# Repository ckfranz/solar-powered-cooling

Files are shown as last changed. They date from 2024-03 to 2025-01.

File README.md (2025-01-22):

Solar Tracker

# Automated Solar Powered Cooling

The course project involved designing a prototype for a solar tracking solar cell-powered fan cooling system.
<p align="center">
Screenshot 2025-01-21 at 10 57 51 PM
</p>

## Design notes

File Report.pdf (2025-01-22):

## SYDE 361

Nicholas Barton (20877569), Jack Eshkenazi (20893647), Greg Fouzie (20889968), Curtis Franz (20831938), Azaan Wazir (20877312)

## Prototype - Solar Panel Powered Fan Components 2-4

SYDE361-S2023 2

Component 2: Insights

Insight #1: When building the initial prototype, there was an issue of there not being enough space to place all electrical components securely within the product.

Method: The design team was able to find this issue by initially attempting to place all the components and seeing that they did not all fit.

Application: The team measured the dimensions of all the components to see if there was any feasible method to place all the parts within the container. Realizing that the electrical components did not all fit in the design, the team decided to redesign the electrical container. The container was bound horizontally such that it had to fit within an existing piece, so the piece was expanded vertically to allow more components to sit inside. This insight applies to the project as this forced a change to the aesthetics of the design. Previously, the component box was small and didn’t stick out when being used, but now with the longer container the electrical container stuck out. The team could address this in later design iterations by making the bounding component larger horizontally or extending the container base vertically such that when tilted the electrical container doesn’t stick out.

Insight #2: The initial fan cage that was designed was no longer required for the prototype.

Method: The team found the originally designed fan cage to be unnecessary, due to the fan being slow and therefore not harmful to the user. This was discovered by gradually increasing the fan speed through increasing current and testing the force exerted on the test user’s hands. Once the upper bound of the producible fan speed was reached, the team was able to derive that it wouldn’t cause any pain when interacting with the fan.

Application: This insight was useful for the project to help simplify the physical complexity of the design and allow for the product to be built in the limited time that was given. In future designs and iterations, the team will need to find out the theoretical max current output of the panel and the max rotations per minute of the fan in the final design. Using research and analysis the team can find out whether the fan will be damaging or dangerous to the user. The fan cage will then be implemented as planned should there be any danger.

Insight #3: The summer season tilt angle of the solar panel could not be reached using the device which did not properly allow the solar panel to have the correct tilt angle for all seasons.

Method: The team was able to find this issue during the initial testing. When the team attempted to test all the seasonal configurations (tilt angles) of the solar panel, the rotation of the solar panel was blocked due to its platform being too long. This led to the rotation being stopped and the summer tilt angle being unreachable.

Application: This insight applies to the project since it directly impacts the design of the prototype. This impacted the design by forcing the team to decrease the solar panel platform length. The redesign did not change the overall look of the design, but it did make it harder to attach pieces together. The surface area for the command strips was smaller which led to having less grip between the components. Overall, the prototype still functioned reliably, but for future iterations where parts could be scaled, all tilt angles should be simulated before being tested physically to ensure functionality without risking redesign.

Component 3: Prototype Verification

The principal objective of data collecting was to gain insight in two particular areas. The first was to determine the degree to which different levels of cloud cover affect the maximum theoretical power output. The second was to determine how light-based tracking affects the maximum theoretical power output.

Three unique sets of data were collected (Table 3.1). All tests were performed at the same picnic bench near the north entrance to E5. In each test, the system was placed on top of the picnic bench such that the solar panel was exposed to the sky with no obstructions. The angle of elevation of the solar panel was set to 20° which corresponds to the 4th position of the adjustment wheel, optimal for June-September in Waterloo (see figure 4.1). Finally, a fine sampling period of 0.5 seconds was used to capture transient changes in the metrics being collected.

Table 3.1 - Testing Conditions

| Test 1 | Test 2 | Test 3
Date. time | 13/07/23, 2:30-3 pm | 16/07/23, 2:30-3 pm | 16/07/23, 3-3:30 pm
Sun condition | Cloudy | Partly Sunny/Hazy | Partly Sunny/Hazy
Tracking System | Single Axis Tracking | Single Axis Tracking | Fixed

Figure 3.1 compares the maximum theoretical power yields of the solar panel in cloudy versus sunny conditions. From about 2:30 to 2:57 pm, there is a significant amount of variation in maximum theoretical power yields in both plots due to transient changes in the sun conditions due to clouds and cloud breaks. However, from 2:43 to 2:57 pm there is a clear disparity in maximum theoretical power yields. During this timeframe, the respective sun conductions held mostly steady. Here, test 2 (mostly sunny conditions) had theoretical power yields of approximately 250mW, around 5x, the theoretical power yields of test 1 (mostly cloudy conditions), which hovered around 50mW. This deviation shows how significantly power yields are affected by cloud conditions. This information would be useful to communicate to users in a user manual to inform them when and what sun conditions the system can realistically be used to power the fan. This result would also be valuable to consider in future design iterations in the development of power-saving features.

Interestingly, there are a couple of maximum theoretical power spikes in the test 1 plot where the sun broke out. At 2:58 pm the theoretical maximum power levels reached a peak of 551mW. This exceeded the maximum theoretical power observed over the entire duration of test 2 (mostly sunny conditions), due to some haziness during test 2.

Figure 3.2 compares the maximum theoretical power yields of the solar panel with and without single-axis tracking. In test 2, the panel utilizes a pair of photoresistors to orient the panel such that it receives optimal light exposure. While the first 13 minutes of test 2 depict varying sun exposure due to fleeting clouds, the maximum theoretical power peaks over the course of the entire interval remain fairly steady (around 250mW). In test 3, the panel was fixed at the optimal azimuth the moment the testing interval began. As time passed and the sun’s azimuth changed, the panel’s angle became increasingly divergent. The plot for test 3 initially shows a steady maximum theoretical power yield until around 3:18 pm at which point it steadily drops. This suggests that using a single-axis tracking system is indeed beneficial, as it results in steadier maximum theoretical power yields.

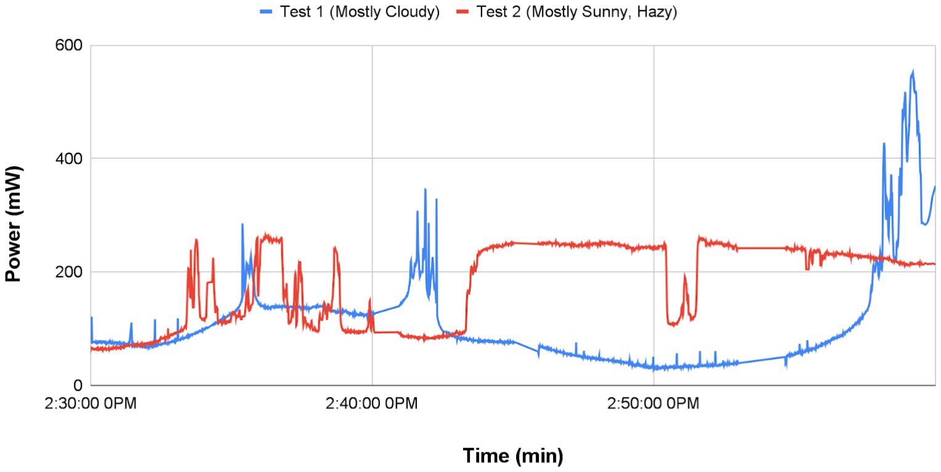
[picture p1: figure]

Figure 3.1 - Theoretical maximum power yields of the solar panel in cloudy versus sunny conditions

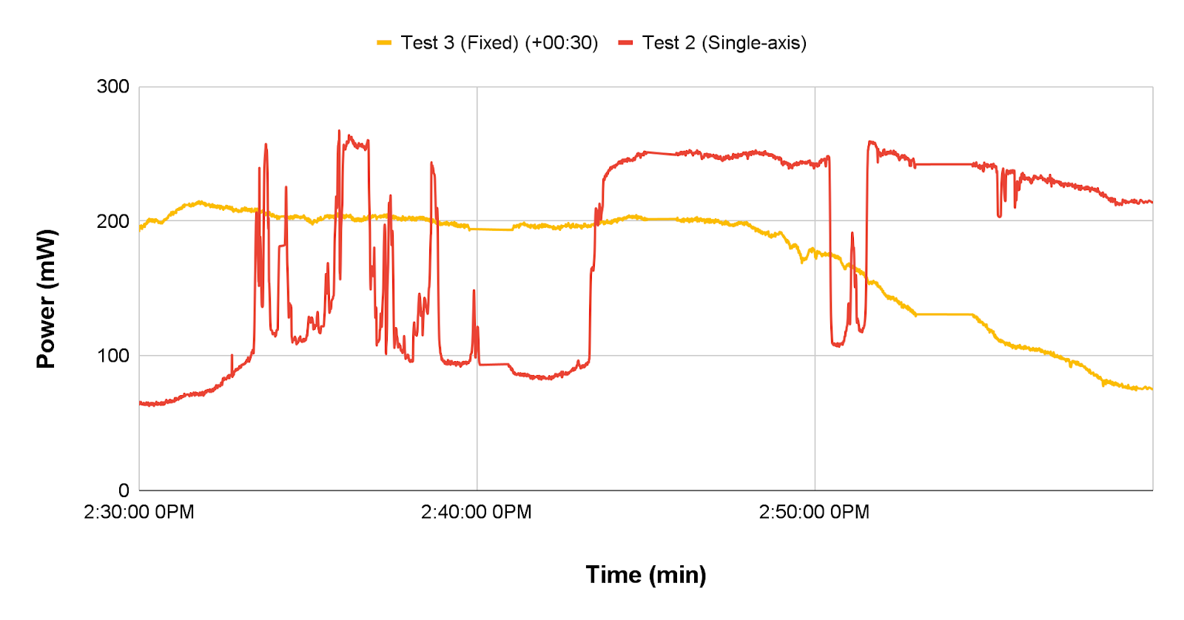
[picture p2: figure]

Figure 3.2 - Theoretical maximum power yields of the solar panel with and without single-axis tracking

Unfortunately, there were several limitations in the testing methodology used for data collecting. Some of these include the uncontrollable variations in weather and sun conditions, having collected data on different days, testing periods limited to 30 minutes, testing limited to a single location and time period, etc.

Component 4: Design Documentation

A) Electronic Hardware:

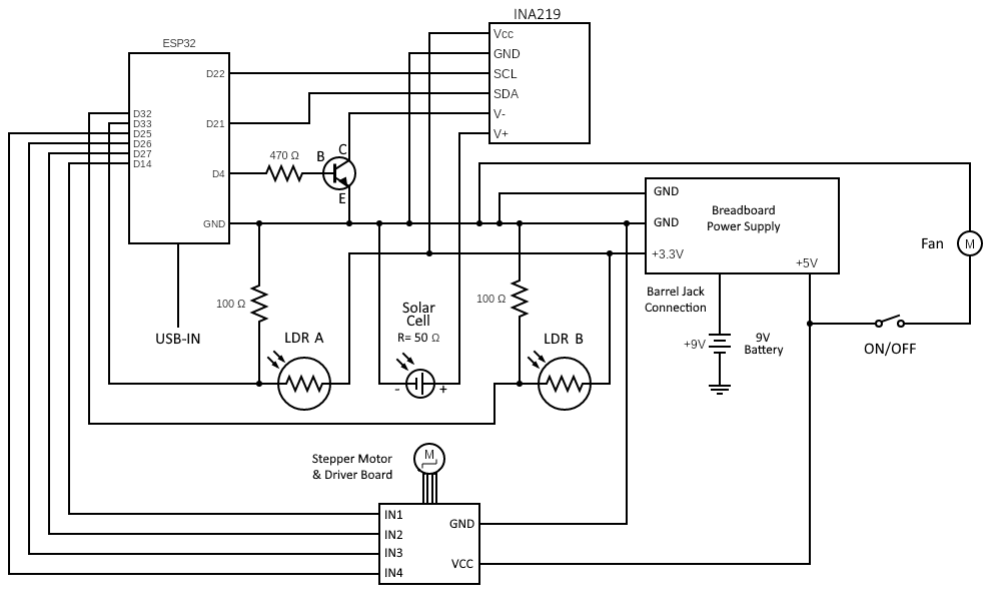
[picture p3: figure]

Figure 4.1 - Fully labeled schematic including all components of the prototype

Photoresistors/LDRs: The photoresistors or light-dependent resistors (LDR) change their resistance depending on how much light they receive. This serves the purpose of calibrating the direction of the solar panel and tracking the sun throughout the day. Two LDRs are angled and pointed in opposite directions so they can detect the light from both sides of the solar panel. When one detects more light than the other, the code instructs the motor to move in the direction of the LDR that is detecting more light. This is how they are used to track the point of maximum power from the sun and get the maximum amount of power throughout the day. 100Ω Pull-down Resistors: One 100Ω pull-down resistor is placed in series with each LDR to allow the light data to be read by the microcontroller. To get the data from the LDRs, the voltage is measured across the 100Ω resistor. When it is bright, the resistance of the LDR drops which creates an increase in voltage across the pull-down resistor. This higher voltage reading indicates an increase in light detected by the LDR. This makes the 100Ω resistors essential for light detection in the prototype.
9V Battery: The 9V battery supplies power to the breadboard power supply which regulates the voltage and supplies both 3.3V and 5V to the components that need it. In later stages of the prototype, this battery would ideally be charged by the solar panel.
5V DC Motor: The 5V DC motor takes in 5V of power and turns a shaft that a fan blade is attached to. The motor rotates the fan blades quickly to cool the user on a hot and sunny day. ON/OFF Switch: The ON/OFF switch is used to turn the fan on and off. If the user does not need the fan and wants to conserve power, they can turn the fan off and then back on when needed again with ease.

Power Estimation:
The average power consumption used by the circuit is measured by summing the average current draw from each component in the entire system.

ESP32: When the ESP32 is in active mode, it draws an average of 240mA of current. Since the ESP32 is always in active mode in the system, it continuously draws 240mA of current. INA219: From the INA219 datasheet, it takes a supply voltage of 3.3V and has a maximum current draw of 1mA. Since this value is low compared to the rest of the system the maximum current draw can be used in the estimation.
LDRs & Pull-down Resistors: Since the resistance and therefore current draw changes based on the light the LDRs receive, the current estimation will be measured in sunny conditions since that is when the system is most useful. In sunny conditions, the average current draw from both LDRs and both pull-down resistors was measured to be about 2.5mA each.
DC Motor: The DC motor, when powered on, was measured to consume an average of 417mA of current. However, it is hard to predict how often the user will have the fan on, since that is up to the user. Therefore, two power estimates will be made, one with it on and one with it off. Stepper Motor: The 28BYJ-48 stepper motor typically draws about 240mA when powered on. In the system, outputs are disabled when it is not moving to save power. The ESP32 polls both LDRs every 15s but the motor does not necessarily move every time it polls. Therefore from observation during data collection, the motor activates about every 10 mins for around 5 seconds making the average power consumption 240*5/600 = 2mA.
Transistor: The transistor consumes very little current in the system, the base current was measured to be around 0.02mA which is very small and can therefore be neglected. The collector current was neglected as well.

After summing the current consumption from every component, the total power or current consumption of the system is 665mA when the fan is on and 248mA when it is off.

Possible approaches for reducing power consumption include putting the ESP32 in sleep mode when not polling or moving the motor. Since it is not necessary to get data from the current sensor at every second when not gathering data, the ESP32 can be put in Modem Sleep mode. In Modem Sleep mode, everything is active except for the Wi-fi, Bluetooth and the radio. When not gathering data, those three functionalities of the ESP32 are not necessary and the ESP32 can consume significantly less power. In Modem Sleep mode, the ESP32 only consumes 3mA at low speeds reducing about 237mA of current draw.

The other approach to reducing power consumption is setting a limit to how long the user can use the fan. The majority of the power consumption in the system is done by the DC motor that the fan is attached to. To reduce power consumption during future design iterations, the team can explore ways to limit the power used by the fan. This can be done by limiting the current and thus lowering the intensity of the fan when on for longer periods of time. This unfortunately does negatively impact the user’s experience and should be avoided unless completely necessary.

B) Microcontroller Software

The code that was run by the ES32 needed to accomplish two things: It needed to turn the stepper motor in a manner which tracked the sun, and it needed to monitor the current and voltage outputs from the solar panels. The code's secondary objective was to do all this using as little power as possible.

In order to track the movements of the sun, the code utilized a simple algorithm which used the photoresistor outputs as input. This algorithm was called during the “unmoved” mode of the prototype, and it worked in the following way: If the right photoresistor had a higher light intensity value than the left, then it turned right and if the left value was higher then it turned left. As soon as the code noticed that the left and right values were equal it stopped rotating. The photoresistor light intensity values were quantized into bigger buckets than the units they were measured in, meaning that there was a leniency of plus/minus 35 units. For example, if the right photoresistor’s value is less than 35 units apart from the left photoresistor’s value, they are considered equal. It was necessary to have the photoresistors facing different angles because otherwise, they would always have the same output from the sun since it is so far away that its rays are essentially parallel to both of them.

Upon initially booting up, the code starts off in the “unmoved” state, which pings the outputs of the photoresistors every 30 milliseconds. It takes an average of 20 samples of these outputs before deciding to make a movement with the motor, which adds up to a call to the stepper object every 0.6 seconds. Since we used the “moveTo” method however, the motor wouldn’t appear to stop moving instantaneously, only accelerate and then decelerate quickly once it found the most favorable point. Once the system has found the most favourable point, it goes into a new state called “power_save” which only pings the photoresistor outputs every 15 seconds in order to save energy. Upon pinging, if the values are not equal, it would go back into an “unmoved” state and find the optimal positioning once again.

The reason that the ESP32 couldn’t be put into a sleeping mode during our “power_save” state to save even more energy, is that we needed to constantly be tracking solar panel outputs for our testing. In order to measure both voltage and current, we followed closely to the design used in Lab 3, in which we utilized a transistor to change the INA-219 from being in parallel to the solar panel to measure the voltage, to being in series with it to measure its current. These power samples were taken every 30 milliseconds. In order to process this data into the charts shown above, the time stamp, voltage, current, and power (voltage times current) were placed into a comma-separated string sent via serial port to a terminal instance of an app called “CoolTerm” from which it was easy to record them and compile them into a .csv file, and then imported into our spreadsheet application of choice.

C) Interface

The interface for this prototype consists of manual adjustments, buttons, lights, and switches. There is a master power switch with a corresponding light that indicates if it’s on or off, but that interface is relatively simple and should not be used after setting up the prototype. Rather, the focus for this section of the document will be on a manual adjustment component and a switch.

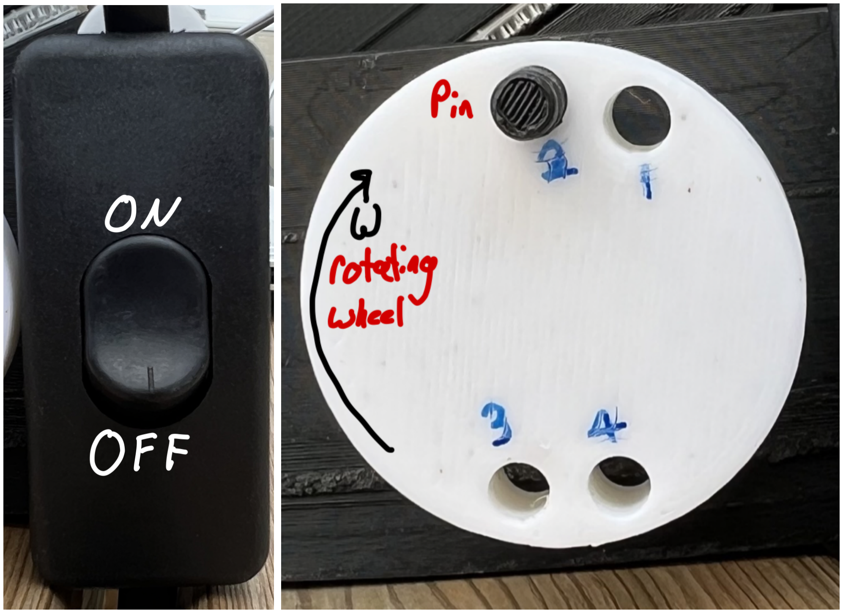
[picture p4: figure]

Figures 5.0, 5.1 - Power Switch and Manual Adjustment Wheel

Firstly, the power switch aims to allow users to control whether the fan is operating or not. If a user switches the interface in one direction, it will result in the fan beginning to move and therefore the system will cool down the user, and switching it in the other direction will turn the fan off. Users will know when the fan is on once they hear the motor and feel the wind from the blades and they will know when it turns off via the opposite indications.

Further, the manual adjustment wheel aims to allow users to adjust the elevation of the solar panel and therefore optimize the current output based on the month of the year. Theoretically, users would receive a manual when purchasing the fan and it would contain instructions for setting up the wheel. Different months of the year are approximated to have optimal elevation angles of 20° (June-September), 35° (May, October), 50° (April, November), and 65° (December-March) degrees which correspond to holes 4, 3, 2, and 1 respectively. Users can change the setting by removing the pin and then rotating the white wheel to the desired pin, and then sliding the pin back in. Users will know that they have successfully changed the elevation angle when the hole is correct according to the current month in the manual, and the pin is back in a hole such that the wheel no longer rotates.

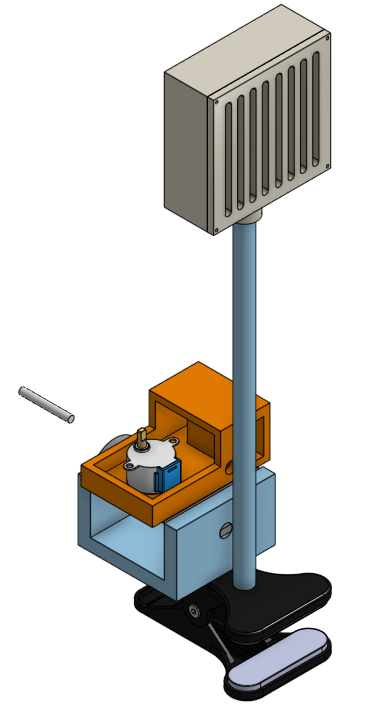
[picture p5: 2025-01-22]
Mechanical Design/Renders/Final Colored Front.png

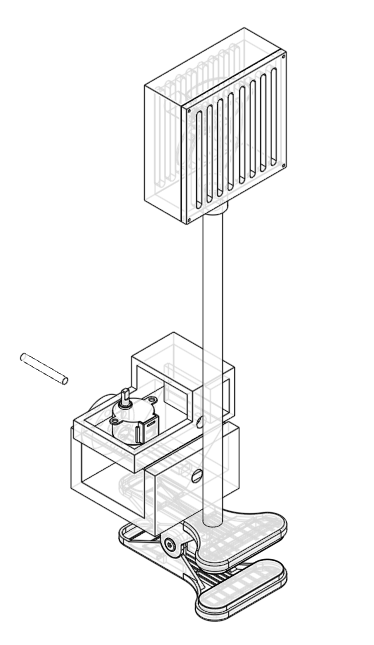
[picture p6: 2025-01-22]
Mechanical Design/Renders/Final Hidden Front.png

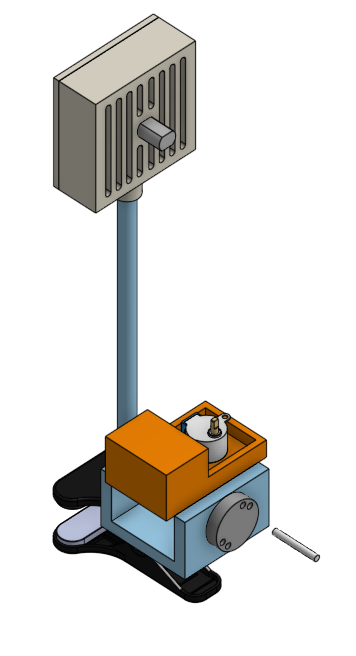
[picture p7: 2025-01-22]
Mechanical Design/Renders/Final Colored Back.png

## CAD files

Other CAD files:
Mechanical Design/Model/Assembly.x_t

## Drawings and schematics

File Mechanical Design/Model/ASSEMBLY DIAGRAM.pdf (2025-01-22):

2
1

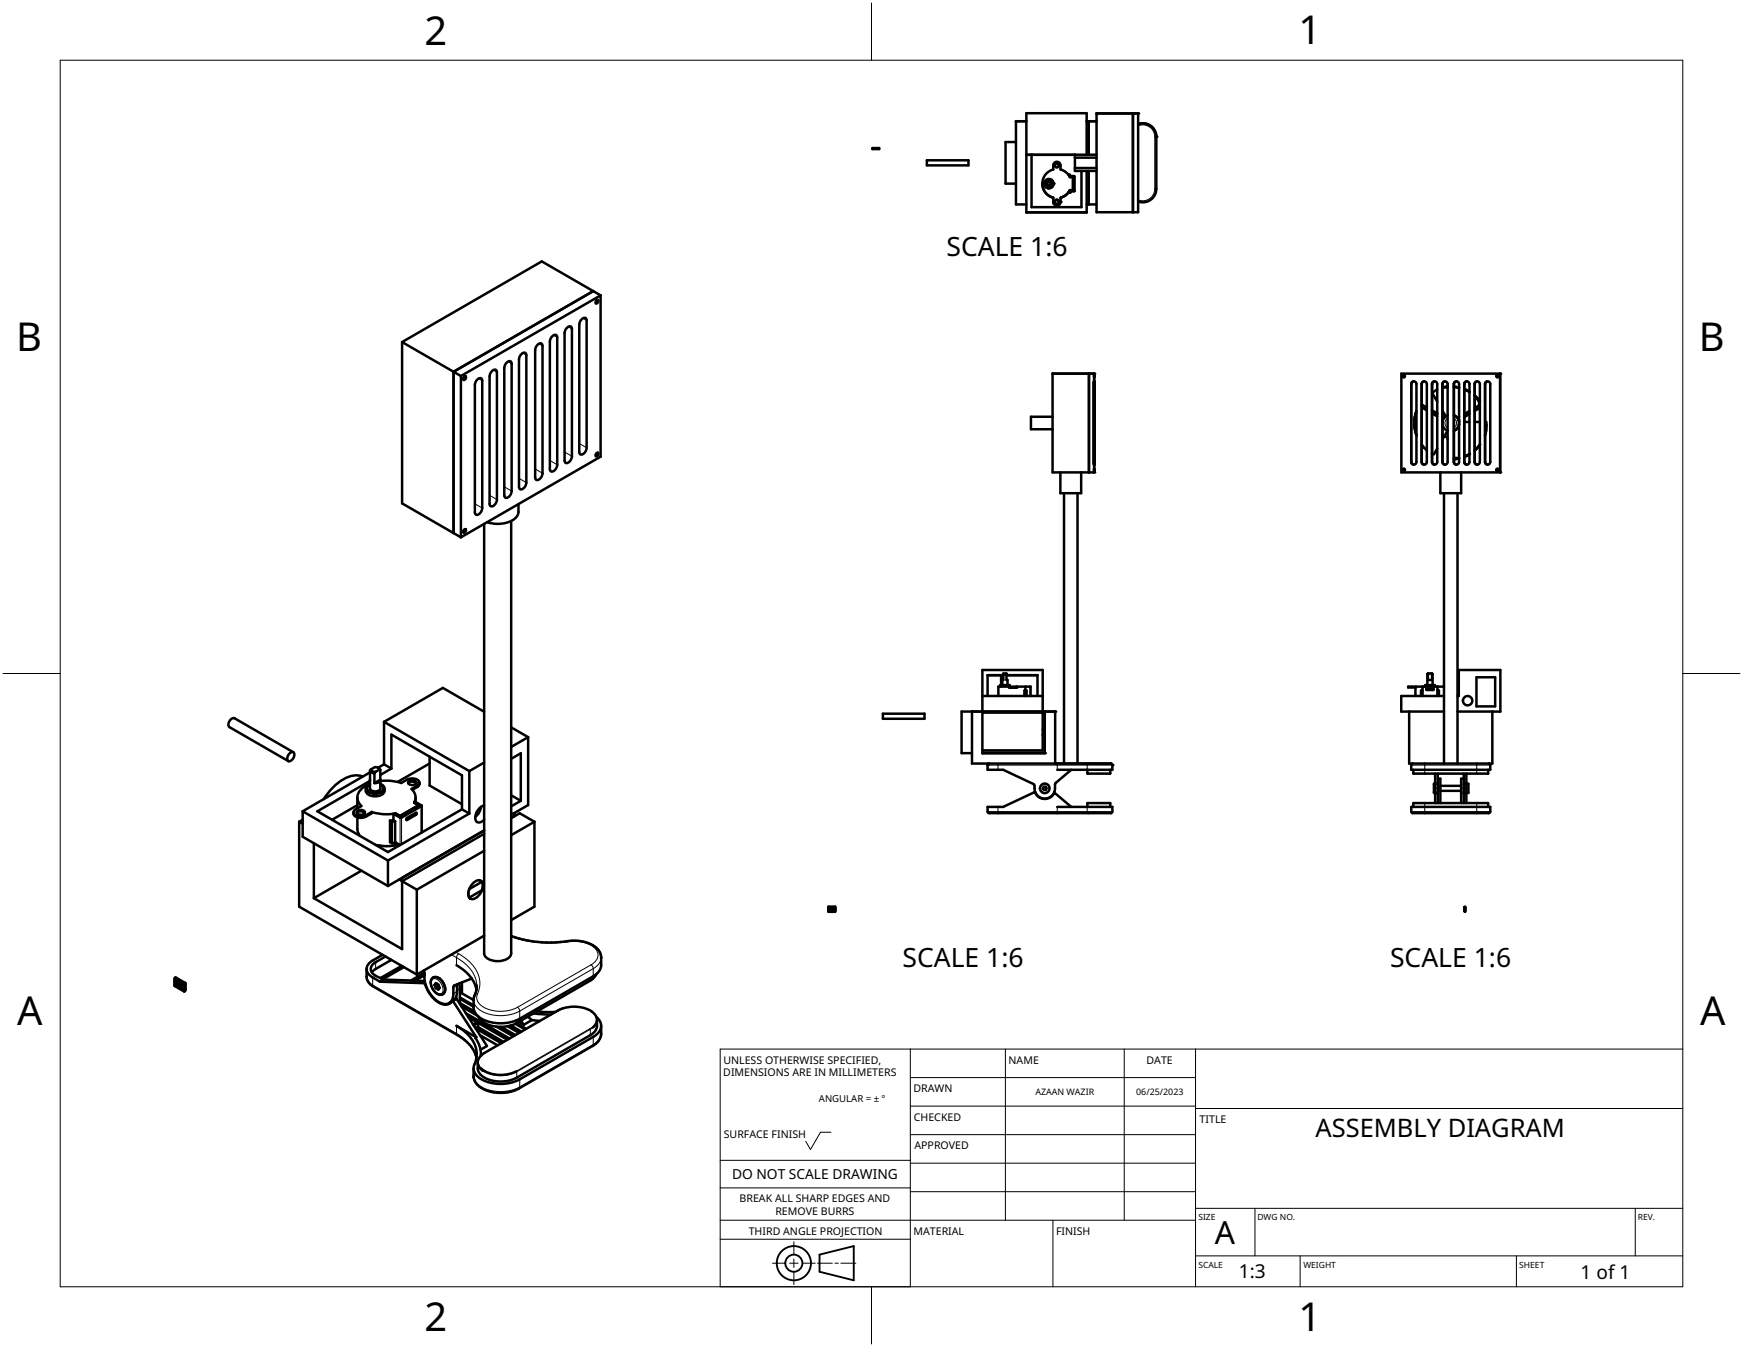
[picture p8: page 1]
MATERIAL; FINISH; SCALE 1:6

UNLESS OTHERWISE SPECIFIED, DIMENSIONS ARE IN MILLIMETERS ANGULAR = ± ° SURFACE FINISH | | NAME | DATE

DRAWN | AZAAN WAZIR | 06/25/2023

CHECKED | | | TITLE ASSEMBLY DIAGRAM

APPROVED

DO NOT SCALE DRAWING

BREAK ALL SHARP EDGES AND

REMOVE BURRS
THIRD ANGLE PROJECTION

SIZE A | DWG NO. | REV.

SCALE 1:3 | WEIGHT | SHEET 1 of 1

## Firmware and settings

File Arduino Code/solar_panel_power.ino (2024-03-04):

/*
* This ESP32 code is created by esp32io.com
*
* This ESP32 code is released in the public domain
*
* For more detail (instruction and wiring diagram), visit https://esp32io.com/tutorials/esp32-light-sensor
*/

#include <AccelStepper.h>
#include <Wire.h>
#include <Adafruit_INA219.h>

// REMEMBER TO CHANGE PINS ACCORDINGLY :)
#define LIGHT_SENSOR_PIN_A 33 // ESP32 pin for first photoresistor
#define LIGHT_SENSOR_PIN_B 32 // ESP32 pin for second photoresistor

#define pin1 14
#define pin2 27
#define pin3 26
#define pin4 25

// INA SOLAR PANEL SETUP
Adafruit_INA219 ina219;

// Define pin
int base = 4;
// Reporting frequency
float freq = 2; // Hz
// Delay after changing state of transistor
int del = 2;
// Sensor variables
float current_mA = 0;
float voltage = 0;
float power_mW = 0;
// Tracking time
unsigned long last = 0;
unsigned long led_last = 0;
float t = 0;
int led = 2000;
bool state = false;

// STEPPER MOTOR SETUP
AccelStepper stepper(AccelStepper::FULL4WIRE, pin1, pin3, pin2, pin4);
int incomingAngle;
double degreesPerStep = 5.625 / 64;
// Average tracking
int left_sum = 0;
int right_sum = 0;
int average_left = 0;
int average_right = 0;
// Time tracking
int counter = 0;
int sample_length = 20;                // Number of 30 milliseconds used for average
int power_save_sample_length = 500;    // 15 seconds
// State variables
bool has_moved = false;
bool power_save = false;

void setup() {
    // REMEMBER TO CHANGE BAUD RATE OF SERIAL MONITOR TO 9600 :)
    Serial.begin(9600);

    // INA SOLAR PANEL
    pinMode(base, OUTPUT);
    pinMode(2, OUTPUT);
    while (!Serial) {
        Serial.println("Starting...");
        delay(1);
    }

    if (!ina219.begin()) {
        Serial.println("Failed to find INA219 chip");
        while (1) {
            delay(10);
        }
    }

    ina219.setCalibration_16V_400mA(); // Use 16V, 400mA range

    last = millis();
    led_last = millis();

    // STEPPER MOTOR
    stepper.setMaxSpeed(4096);
    stepper.setAcceleration(40);
}

void loop() {
    int right_photo_res = analogRead(LIGHT_SENSOR_PIN_A);
    int left_photo_res = analogRead(LIGHT_SENSOR_PIN_B);

    left_sum += left_photo_res;
    right_sum += right_photo_res;

    if (counter == sample_length && power_save == false) {
        average_left = left_sum / sample_length;
        average_right = right_sum / sample_length;

        if (average_left > average_right + 70) {
            stepper.moveTo(stepper.currentPosition() - (6 / degreesPerStep));
            has_moved = true;
        } else if (average_left > average_right + 35) {
            stepper.moveTo(stepper.currentPosition() - (3 / degreesPerStep));
            has_moved = true;
        } else if (average_right > average_left + 70) {
            stepper.moveTo(stepper.currentPosition() + (6 / degreesPerStep));
            has_moved = true;
        } else if (average_right > average_left + 35) {
            stepper.moveTo(stepper.currentPosition() + (3 / degreesPerStep));
            has_moved = true;
        } else {
            stepper.stop();
            if (has_moved == true) {
                power_save = true;
                stepper.disableOutputs();
            }
        }

        left_sum = 0;
        right_sum = 0;
        counter = 0;
    }

    if (power_save == false) {
        stepper.run();
    }

    if (millis() - last > 1000.0 / freq) {
        last = millis();
        t = last / 1000.0;

        digitalWrite(base, HIGH);
        delay(del);
        current_mA = ina219.getCurrent_mA();
        digitalWrite(base, LOW);
        delay(del);
        voltage = ina219.getBusVoltage_V();
        delay(del);

        power_mW = (0.7 * voltage) * current_mA;

        Serial.print(t);
        Serial.print(", ");
        Serial.print(voltage);
        Serial.print(", ");
        Serial.print(current_mA);
        Serial.print(", ");
        Serial.println(power_mW);
    }

    if (millis() - led_last > led) {
        state = !state;
        digitalWrite(2, state ? HIGH : LOW);
        led_last = millis();
    }

    if (counter == power_save_sample_length && power_save == true) {
        counter = 0;
        power_save = false;
        has_moved = false;
    }

    counter += 1;
    delay(30);
}
